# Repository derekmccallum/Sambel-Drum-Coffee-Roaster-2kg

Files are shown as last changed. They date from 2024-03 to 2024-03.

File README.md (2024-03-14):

# Sambel-Drum-Coffee-Roaster-2kg
Open-source design for a 1-2Kg drum roaster.<br>
Refer:<br>
https://homeroasters.org/forum/viewthread.php?thread_id=4802<br>
https://3dwarehouse.sketchup.com/model/95658df4-883a-404a-b0dc-fe69c1a740fb/Coffee-Roaster<br>

Samble Coffee Roaster - 3D Warehouse

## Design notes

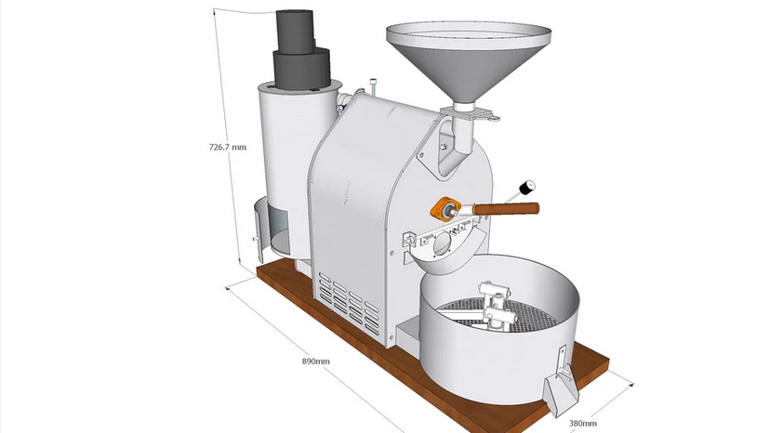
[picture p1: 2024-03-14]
Samble Coffee Roaster - 3D Warehouse.png

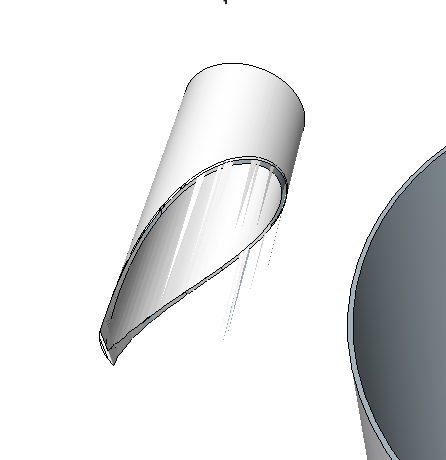
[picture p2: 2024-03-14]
Notch Templates - 20180130/CycloneDraw Notch 1_IMAGE_PASTED_FROM_CLIPBOARD_INTO_SOLID_EDGE_2.bmp

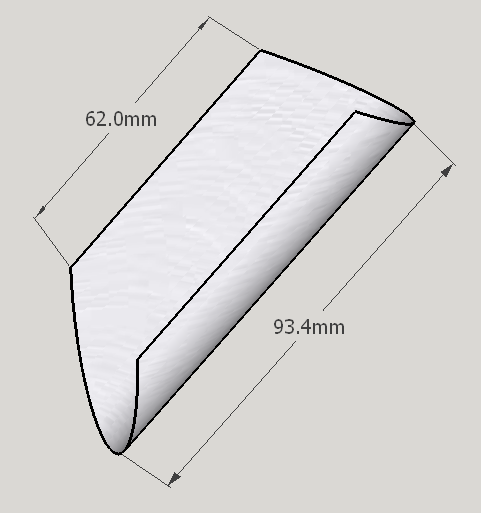
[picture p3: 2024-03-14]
Notch Templates - 20180130/Tube Notch Template 3_IMAGE_PASTED_FROM_CLIPBOARD_INTO_SOLID_EDGE_2.bmp

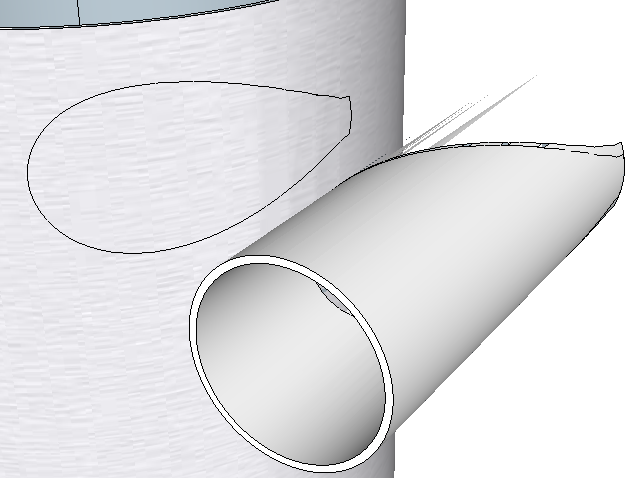
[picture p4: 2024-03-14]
Notch Templates - 20180130/CycloneDraw Notch 2_IMAGE_PASTED_FROM_CLIPBOARD_INTO_SOLID_EDGE_2.bmp

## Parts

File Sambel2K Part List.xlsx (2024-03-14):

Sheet: Costing
ROASTER COMPONENT LIST
Group | Component | Source | Unit Cost (exVAT) | Qty | Total (exVAT)
Body | 2 BOLT FLANGE BEARING UNITS | http://www.wychbearings.co.uk/ucfl201_housed_bearing_ldk.html | £8.67 | 2 | £17.34
 | Plate Jointing Rods |  |  |  | £0.00
 | Mild Steel Cutting & Fabrication |  |  |  | £0.00
 |  | https://www.metals4u.co.uk/mild-steel/tube/tube/3-x-16-swg/p2350
 | Cooling Tray Draw Tube - 2" (50.8mm OD) x 16 swg Mild Steel Tube
 | Drum Draw Tube - 1 3/4" (44.5mm OD) X 16 swg Mild Steel Tube | https://www.metals4u.co.uk/mild-steel/tube/tube/1.34-x-16-swg/p2343 | £8.85 | 1 |  | £17.34
Motors | Drum Blower Motor
 | Cooling Tray Motor
 | Drum Motor & Gear Box | http://www.ggm.co.kr/eng/product/ac/AC_TerminalBoxInduction_15W.asp | £85.25 | 1 | £85.25 | £85.25
Chain Drive | 31-17 Sprocket - 3/8" Pitch Simplex 17 Teeth - Taper Bush Ref 1008 | http://www.wychbearings.co.uk/sprockets/31-17_sprocket_taper_bush.html | £5.05 | 2 | £10.10
 | 1008 Taper Bush - Metric Shafts (10mm) | http://www.wychbearings.co.uk/taper_bushes/1008-10.html | £3.05 | 1 | £3.05
 | 1008 Taper Bush - Metric Shafts (12mm) | http://www.wychbearings.co.uk/taper_bushes/1008-12.html | £3.05 | 1 | £3.05
 | British Standard 06B Simplex Roller Chain - 1 Metre Length + Conn Link | http://www.ebay.co.uk/itm/British-Standard-05B-to-12B-Simplex-Roller-Chain-1-Metre-Length-Conn-Link-/161406512840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 | £7.60 | 1 | £7.60
 |  |  |  | 1 | £0.00 | £23.80
CPU |  |  |  |  | £0.00
 |  |  |  |  | £0.00
Sensors
 |  |  |  |  | £126.39

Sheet: Part Listing
Part # | Zone | Description | Material | Stock | Thickness | Unit Count | Laser/Fabricate/Procured | Supplier | Drawing File | Drawing File Format
1 | Roast Chamber | Roaster Front Plate | Mild Steel | Sheet | 5mm | 1 | Laser | TBD
2 | Roast Chamber | Roaster Drum Door | Mild Steel | Sheet | 5mm | 1 | Laser | TBD
3 | Roast Chamber | Roaster Rear Plate | Mild Steel | Sheet | 5mm | 1 | Laser | TBD
4 | Roast Chamber | Roaster Drive Motor Plate | Mild Steel | Sheet | 5mm | 1 | Laser | TBD
5 | Roast Chamber | Drum Door Cover | Stainless Steel 304 | Sheet | 1.5mm | 1 | Laser | TBD
6 | Roast Chamber | Drum Door Fasteners A | Stainless Steel 304 | Sheet | 3mm | 2 | Laser | TBD
7 | Roast Chamber | Drum Door Fasteners B | Stainless Steel 304 | Sheet | 3mm | 2 | Laser | TBD
8 | Roast Chamber | Drum Cylinder | Mild Steel | Sheet | 3mm | 1 | Ext-Fabricated | TBD
9 | Roast Chamber | Heat Shield Front | Stainless Steel 304 | Sheet | 0.7mm | 1 | Laser | TBD
10 | Roast Chamber | Heat Shield Rear | Stainless Steel 304 | Sheet | 0.7mm | 1 | Laser | TBD
11 | Roast Chamber | Burn Chamber Cover | Stainless Steel 304 | Sheet | 0.5mm | 1 | Laser | TBD
13 | Roast Chamber | Body Cover Mount End | Mild Steel | Sheet | 5mm | 4 | Laser | TBD
14 | Roast Chamber | Body Cover Mount Mid | Mild Steel | Sheet | 5mm | 2 | Laser | TBD
15 | Roast Chamber | Drive Collar Drum Supt Front | Stainless Steel 304 | 30mm Round Bar |  | 1 | Ext-Fabricated | TBD
16 | Roast Chamber | Drum Stays | Stainless Steel 304 | 5mm Round Bar |  | 4 | Ext-Fabricated | TBD
17 | Roast Chamber | Drum Drive Shaft | Stainless Steel 304 | 12mm Round Bar |  | 1 | Ext-Fabricated
18 | Roast Chamber | Drum Door Shaft | Stainless Steel 304 | 8mm Round Bar |  | 1 | Ext-Fabricated
19 | Roast Chamber | Hopper Face Plate | Stainless Steel 304 | Sheet | 4mm | 1 | Laser | TBD
20 | Roast Chamber | Hopper Side Panel | Stainless Steel 304 | Sheet | 1.5mm | 2 | Laser | TBD
21 | Roast Chamber | Body Plate Shafts ShortFront | Stainless Steel 304 | 11mm Hex Bar |  | 4 | Ext-Fabricated
22 | Roast Chamber | Body Plate Shafts ShortRear | Stainless Steel 304 | 11mm Hex Bar |  | 4 | Ext-Fabricated
23 | Roast Chamber | Body Plate Shafts Long | Stainless Steel 304 | 11mm Hex Bar |  | 2 | Ext-Fabricated
24 | Roast Chamber | Body Cover Mount Spacer Nut | Stainless Steel 304 | 11mm Hex Bar |  | 12 | Ext-Fabricated
25 | Cyclone | Cooling Tray Draw Gate Valve TBB | Stainless Steel 304 | Sheet | 3mm | 1 | Laser
26 | Cyclone | Cooling Tray Draw Gate Valve TBT | Stainless Steel 304 | Sheet | 3mm | 1 | Laser
27 | Cyclone | Cooling Tray Draw Gate Valve Shut | Stainless Steel 304 | Sheet | 3mm | 1 | Laser
28 | Cyclone | Cooling Tray Draw Gate Valve IN | Stainless Steel 304 | Sheet | 3mm | 1 | Laser
29 | Roast Chamber | Hopper Gate TB | Stainless Steel 304 | Sheet | 3mm | 2 | Laser
30 | Roast Chamber | Hopper Gate IN | Stainless Steel 304 | Sheet | 3mm | 1 | Laser
31 | Roast Chamber | Hopper Gate Shut | Stainless Steel 304 | Sheet | 3mm | 1 | Laser
32 | Roast Chamber | Roast Chamber Air-Draw Fix Plate | Stainless Steel 304 | Sheet | 1.5mm | 1 | Laser
33 | Roast Chamber | Cooling Air-Draw Fix Plate | Stainless Steel 304 | Sheet | 1.5mm | 2 | Laser
34 | Roast Chamber | Burner Mount Plate | Stainless Steel 304 | Sheet | 1.5mm | 1 | Laser
35 | Roast Chamber | Drum Vane Inside | Mild Steel | Sheet | 1.5mm | 4 | Laser
36 | Roast Chamber | Drum Vane Outside | Mild Steel | Sheet | 1.5mm | 4 | Laser
37 | Roast Chamber | Damper Guage Face | Stainless Steel 304 | Sheet | 1mm | 1 | Laser
38 | Roast Chamber | Damper Guage Indicator | Stainless Steel 304 | Sheet | 0.5mm | 1 | Laser
39 | Roast Chamber | Roast Flow Damper | Stainless Steel 304 | Sheet | 0.5mm | 1 | Laser
40 | Roast Chamber | Roast Chamber Body Cover | Stainless Steel 304 | Sheet | 0.5mm | 1 | Laser
41 | Roast Chamber | Roast Chamber Body Access | Stainless Steel 304 | Sheet | 0.5mm | 1 | Laser
42 | Roast Chamber | Drum Second Skin | Mild Steel | Sheet | 0.5mm | 1 | Laser
43 | Cyclone | Cyclone Bottom Plate | Stainless Steel 304 | Sheet | 1.5mm | 1 | Laser | TBD
44 | Cyclone | Cyclone Draw Pipe Bottom Plate | Stainless Steel 304 | Sheet | 1mm | 1 | Laser | TBD
45 | Cyclone | Cyclone Thien Baffle | Stainless Steel 304 | Sheet | 0.7mm | 1 | Laser | TBD
46 | Cyclone | Cyclone Top Plate | Stainless Steel 304 | Sheet | 2mm | 1 | Laser | TBD
47 | Cyclone | Cyclone Top Plate Wall Supt | Stainless Steel 304 | Sheet | 1.5mm | 1 | Laser | TBD
~~48~~ | ~~Cyclone~~ | ~~Cyclone Top Plate Edge~~ | ~~Stainless Steel 304~~ | ~~Sheet~~ | ~~1mm~~ | ~~1~~ | ~~Laser~~ | ~~TBD~~
49 | Cyclone | Cylinder body | Stainless Steel 304 | Sheet | 1.5mm | 1 | Ext-Fabricated
50 | Cyclone | Door | Stainless Steel 304 | Sheet | 1.5mm | 1 | Ext-Fabricated
51 | Cyclone | Exit tube | Stainless Steel 304 | Sheet | 1mm | 1 | Ext-Fabricated
52 | Roast Chamber | Vane Support | Stainless Steel 304 | Sheet | 1.5mm | 8 | Laser | TBD
53 | Roast Chamber | Damper Spindle | Stainless Steel 304 | Round | 8mm | 1 | Ext-Fabricated
54 | Roast Chamber | Drive Collar Drum Supt Rear | Stainless Steel 304 | Round | 30mm | 1 | Ext-Fabricated
55 | Roast Chamber | Drive Collar Drum Supt Rear Clamp | Stainless Steel 304 | Sheet | 2mm | 1 | Laser
56 | Roast Chamber | Vane Fixing Tab | Stainless Steel 304 | Sheet | 1mm | 8 | Laser
57 | Roast Chamber | Cabinet cover fixing bottom 1 | Stainless Steel 304 | Sheet | 1.5mm | 2 | Laser
58 | Roast Chamber | Cabinet cover fixing bottom 2 | Stainless Steel 304 | Sheet | 3mm | 2 | Laser
59 | Roast Chamber | Cabinet cover fixing bottom 3 | Stainless Steel 304 | Sheet | 1.5mm | 4 | Laser
60 | Roast Chamber | Cabinet cover fixing middle 1 | Stainless Steel 304 | Sheet | 3mm | 2 | Laser
61 | Roast Chamber | Cabinet cover fixing middle 2 | Stainless Steel 304 | Sheet | 1.5mm | 6 | Laser
62 | Roast Chamber | Cabinet cover fixing middle and top | Stainless Steel 304 | Sheet | 3mm | 2 | Laser
63 | Roast Chamber | Cabinet cover fixing top | Stainless Steel 304 | Sheet | 1.5mm | 6 | Laser
80 | Roast Chamber | 12mm 2 Bolt Flange Bearing |  |  |  | 2 | Procured | http://www.wychbearings.co.uk/lftc12ec_housed_bearing_rhp.html (£45 the pair) http://www.wychbearings.co.uk/ucfl201_housed_bearing_ldk.html or perhaps, http://www.wychbearings.co.uk/lftc12_housed_bearing_rhp.html or even more likely https://www.bearing-king.co.uk/bearing/sf12-rhp/3155 https://www.123bearing.co.uk/housed-bearing-UFL001.php
81 | Roast Chamber | Drum shaft sproket: 31-17 Sprocket - 3/8" Pitch Simplex 17 Teeth - Taper Bush Ref 1008 |  |  |  |  | Procured | http://www.wychbearings.co.uk/31-17_sprocket_taper_bush.html
82 | Roast Chamber | Motor drive sproket: 31-17 Sprocket - 3/8" Pitch Simplex 17 Teeth - Taper Bush Ref 1008 |  |  |  |  | Procured | http://www.wychbearings.co.uk/31-17_sprocket_taper_bush.html
83 | Cooling Tray Driven | Idler drive sprocket: N3/8-10S Rosta 3/8" Pitch Simplex Sprocket Wheel Set for Chain Tensioners |  |  |  |  | Procured | http://www.wychbearings.co.uk/N3-8-10S-ROSTA.html
84 | Cooling Tray Driven | Cooling Tray dive shaft sproket: 31-17 Sprocket - 3/8" Pitch Simplex 17 Teeth - Taper Bush Ref 1008 |  |  |  |  | Procured | http://www.wychbearings.co.uk/31-17_sprocket_taper_bush.html

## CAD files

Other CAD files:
Cutting - 20180130/Sambel2K Roast Chamber and Cyclone 2Dcutting 304Stainless 0.7mm - 20180130.dwg
Fabricating - 20180130/Sambel2K Roast Chamber and Cyclone Fabricated Parts Drum - 20180130.dwg
Notch Templates - 20180130/Tube Notch Template 1.dwg
Cutting - 20180130/Sambel2K Roast Chamber and Cyclone 2Dcutting 304Stainless 3mm - 20180130.dwg
Fabricating - 20180130/Sambel2K Roast Chamber and Cyclone Fabricated Parts Cyclone - 20180130.dwg
Notch Templates - 20180130/CycloneDraw Notch 2.dwg
Cutting - 20180130/Sambel2K Roast Chamber and Cyclone 2Dcutting 304Stainless 2mm - 20180130.dwg
Fabricating - 20180130/Sambel2K Roast Chamber and Cyclone Fabricated Parts Misc1 - 20180130.dwg
Notch Templates - 20180130/Tube Notch Template 2.dwg
Cutting - 20180130/Sambel2K Roast Chamber and Cyclone 2Dcutting 304Stainless 1.5mm - 20180130.dwg
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

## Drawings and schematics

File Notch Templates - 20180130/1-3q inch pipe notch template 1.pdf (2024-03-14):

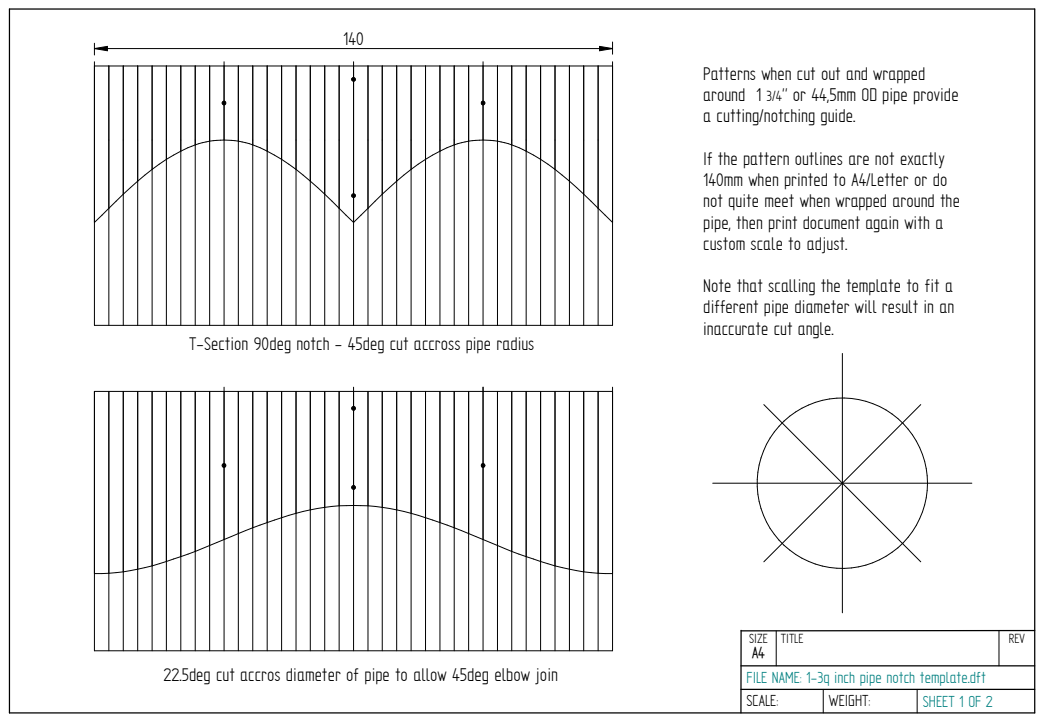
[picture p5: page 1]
TITLE; REV; SCALE:; WEIGHT:; SHEET 1 OF 2

Patterns when cut out and wrapped
around 1 3/4" or 44,5mm OD pipe provide
a cutting/notching guide.

If the pattern outlines are not exactly
140mm when printed to A4/Letter or do
not quite meet when wrapped around the
pipe, then print document again with a
custom scale to adjust.

Note that scalling the template to fit a
different pipe diameter will result in an
inaccurate cut angle.

T-Section 90deg notch - 45deg cut accross pipe radius

SIZE
FILE NAME: 1-3q inch pipe notch template.dft

22.5deg cut accros diameter of pipe to allow 45deg elbow join

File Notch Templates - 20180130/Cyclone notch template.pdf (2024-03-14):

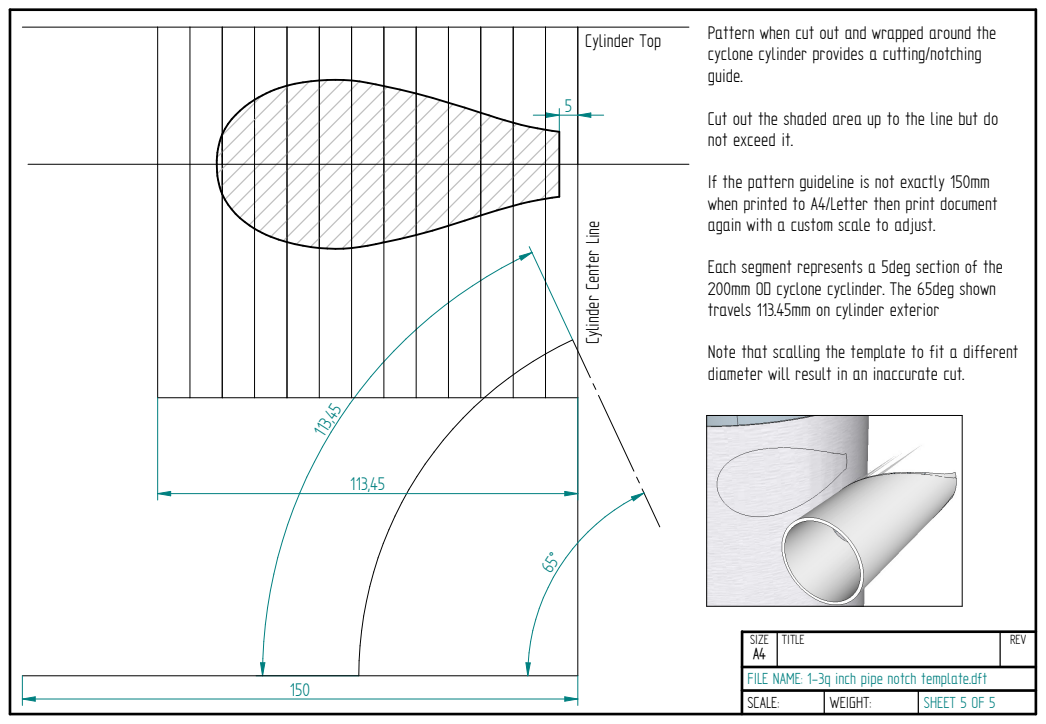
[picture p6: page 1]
TITLE; REV; SCALE:; WEIGHT:; SHEET 5 OF 5; Cylinder Top

Pattern when cut out and wrapped around the
cyclone cylinder provides a cutting/notching
guide.

Cut out the shaded area up to the line but do
not exceed it.

If the pattern guideline is not exactly 150mm
when printed to A4/Letter then print document
again with a custom scale to adjust.

Cylinder Center Line

Each segment represents a 5deg section of the
200mm OD cyclone cyclinder. The 65deg shown
travels 113.45mm on cylinder exterior

Note that scalling the template to fit a different
diameter will result in an inaccurate cut.

SIZE
FILE NAME: 1-3q inch pipe notch template.dft
